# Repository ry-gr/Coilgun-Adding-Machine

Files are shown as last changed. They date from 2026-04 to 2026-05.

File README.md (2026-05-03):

# Coilgun Adding Machine
This is an adding machine, which uses coilguns to carry digits.  
This project was inspired by Matthias Wandel's adding machine, whose posts were an incredible inspiration and resource.  
  
- [Marble adding machine by Matthias Wandel](https://youtu.be/GcDshWmhF4A?si=AagFJ8iIVUzHyiSO)  
- [Further information from his blog](https://woodgears.ca/marbleadd/more.html)  

## TL;DR
The machine is an analog computer that uses marbles to represent bits, and coilguns that shoots the marbles to other columns to carry digits when a bit overflows.  As a note, this project is not finished. I am still working on it actively, but am publishing this preliminarily as my submission for Hack Club: The Game.

## Demo Video (Shows the issue with imprecise positioning)
An issue I am repeatedly running into is having to constantly reposition parts not glued or screw down. I can not get the marble to shoot precisely into the curved part. However this video shows how the logic gates operate and how the machine is capable of charging a capacitor bank, then discharging it by itself. In the video I am performing 1+1 and the marble is unable to properly overflow to get to 2.

https://github.com/user-attachments/assets/430a67ab-8d33-4d41-9ca6-4a4940692cc2

## Schematics

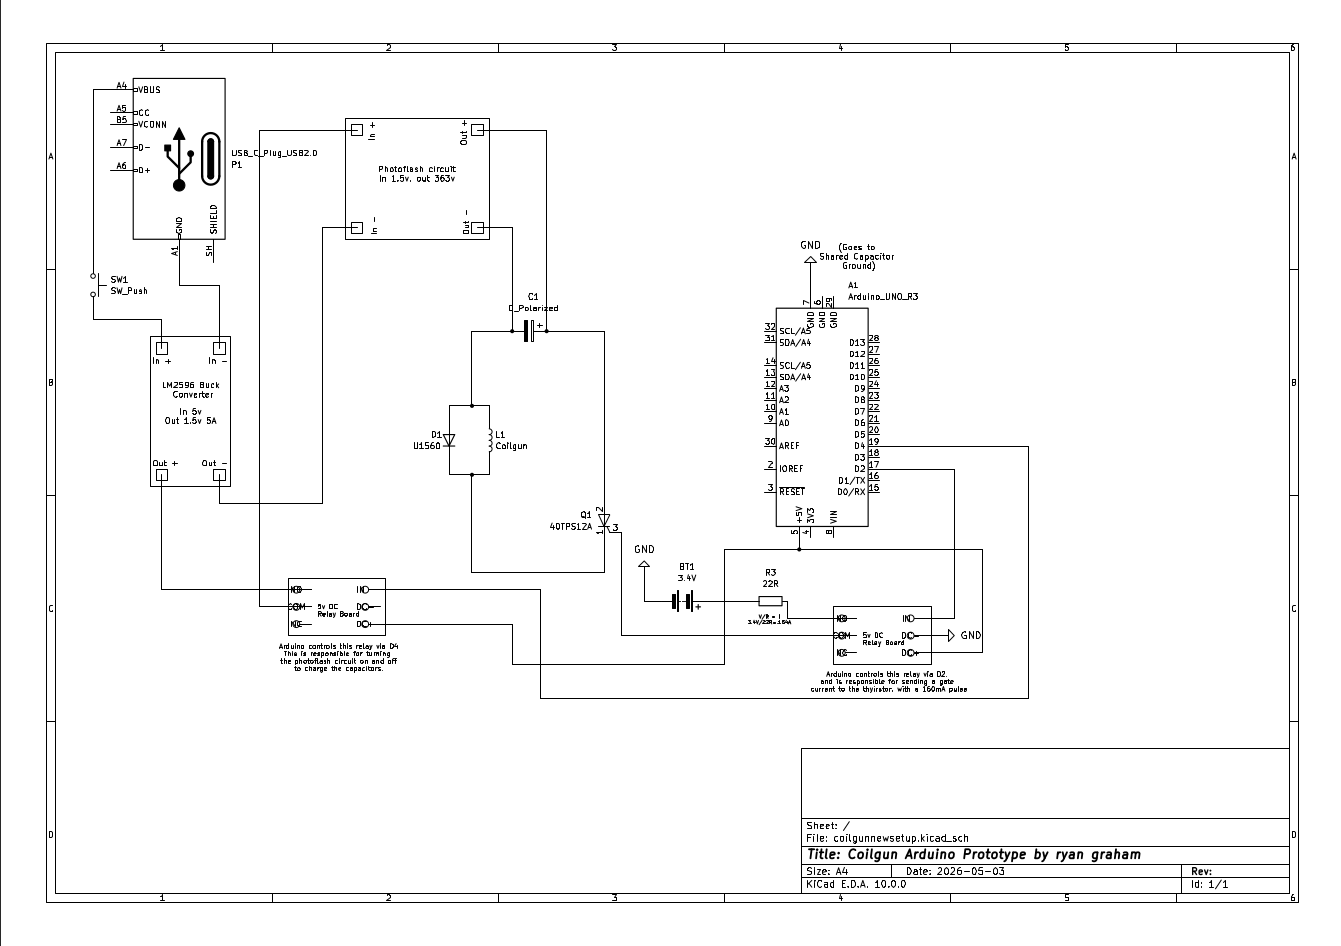
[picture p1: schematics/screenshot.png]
PDF Preview


## FAQ
How does the machine store value?
When the gate is tilted to the left, it has no value. This is the position that all of the gates of the machine start in. 
   
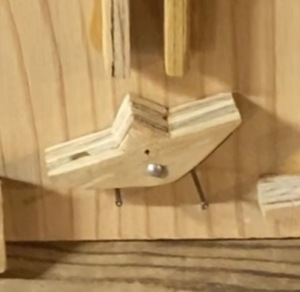
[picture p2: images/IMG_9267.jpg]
noVal


When the gate is tilted to the right, it is storing a value. To determine the value in base 10, you must count how far you are from the far right. The count starts at 0. If this gate was the one furthest to the right, it would be gate 0. 2<sup>0</sup> is 1, so when that gate is tilted to the right, its value is 1. 

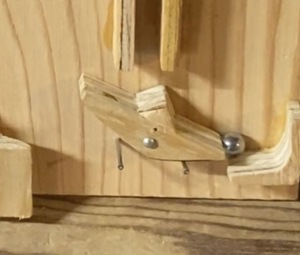
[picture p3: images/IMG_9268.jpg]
holdingVal


# Build Instructions  

> [!CAUTION]
> The voltages needed to accelerate the projectile extremely dangerous and can potentially kill you. I am not saying you shouldn't experiment, but please be very cautious. Have a good multimeter, and know how to use it.

## Part List:
- 40TPS12A Thyristor  
- 2n2222a Transistor  
- 2x 450V 68uF Capacitors  
- USB-C Pinout Board  
- LM2596 Buck Converter (5A)  
- Disposable Camera Flash Circuitry [^1]  
- 24AWG Magnet Wire  
- MUR1560G Diode
- Arduino Uno
- 2x 5v DC Relays  

## How to prepare the disposable camera
You will need to completly strip the disposable camera of its housing, I did this by jamming a flat head screwdriver in the side, cutting all the adhesive holding it together and then popping the clips. The board is basically the only electronic component in the whole thing, so it should be easy to see. You should see a cylindrical capacitor connected to the board. Measure the voltage, and if it is charged (carefully) discharge it with a screwdriver that has a non metallic handle. Then pop out the entire module gently. Mark the board on the connector that the capacitors stripe is. That is the negative output terminal. Now desolder the capacitor, and set it to the side. I did not use the capacitor as it didnt have enough voltage for my project, but it is still a useful component. The next is figuring out how make your board stay triggered. Some have a button that you can pry off, then scratch the pcb coating off to bridge the pins, others you can solder the moveable component in place to permanently set it. 

## Operating Principle of the Electronics
The USB-C is connected to power, supplying 5v, which gets converted to 4.5V with the Buck Converter. This goes to the input of the camera flash circuitry, (technically the flash circuit only accepts 1.5v, but supplying it more makes it charge faster). From there it goes to the capacitors which are wired in parallel to make a 900V Capacitor. Boom, now after about 15seconds of charging we stop, and send a signal from the arduinos digital output. But uh-oh the arduino cant trigger the beefy 40TPS12A by itself, so that gets amplified big time to 200mA with the NPN transistor. Now the signal arrives at the gate, and the once open circuit closes. In an instant the current from the capacitors flows through the thyristor into the coilgun, where it rapidly creates a powerful electromagnetic field around the coil. This Field applies force to the steel .25inch ball sitting at the base of the coil, and the force overpowers gravity accelerating the ball to the coils core. Just as quickly the voltage source shuts off, the capacitors are now empty and the ball flies into the air with velocity. But wait, what about Faradays Principle? With the voltage cut, the coil wants very badly to continue the current it was once conducting so it send a massive voltage spike in the oppposite direction to try to get some more. But now the big boy diode, which is reverse biased awakes from its sleep and the massive voltage spike is consumed as mere heat by the didoe. Just that quickly we have consumed 380V. 


## Operating Principle of the Adding Machine
As explained in Mattias's Video, the machine originally holds 0. Each gate represents a number. Starting from the right, it goes from 2^0, then the gate to its left is 2^1. The one to the left of that is 2^2. This can go on forever. By using the definition of binary numbers, we can add numbers. 
For example: We put a marble into the empty machine on the furthest gate to the right. The rocker tilts and the marble is stuck. The internal value of the machine is now 2^0 = 1. We add a marble to the second gate, and it gets stuck there. By adding this we have added 2^1 = 2, to the internal value of the machine. So in total we have 2+1=3 in value. Now adding another marble to the furthest gate to the right, and whcih tilts the rocker discarding the stuck marble, and shooting the marble to the second gate, which does the same and shoots the marble to the third gate. Now our internal value is 2^2=4. We added 2+1+1, and the machine shows the final value.


## Data Collection and optimization
Coilguns attract ferromagnetic objects to their core while they have current. This is great although if we get our projectile to get attracted to the core, and have velocity but then be pulled backwards by the coilgun. So we need to precisely time when we shut voltage off, so we dont pull our projectile backwards. In lieu of a IR system, to measure the interruption, I decided to precisely time the charging of capacitor, so they will simply run out of voltage when the projectile is at its core and no longer should have an attraction. By measuring the time the projectile charged for, the voltage of the capacitor, and the height the projectile went I came up with this graph. I was charging the capacitors externally with the flash circuit, and manually timing everything, so there might be imprecision, but it gives a rough estimate of where we need to be.  
<sub>A quick note about why I decided to use time instead of voltages to trigger the discharge: I created several iterations of voltage dividers that connected the capacitor to an arduino analog pin. I was able to sucessfully read capacitor voltages, but doing this made a slow bleed from the resistors, which interfered with the charging circuit.</sub>

## Raw Data
| Voltage (V) | Time (sec) | Height (in) |
|---|---|---|
| 363 | 19.63 | 12.5 |
| 469 | 23.54 | 12 |
| 444 | 21.56 | 10 |
| 421 | 20.07 | 10 |
| 375 | 18.38 | 12.5 |
| 408 | 18.71 | 12 |

## Graph


With this data we can conclude somewhere around 18 seconds of charging gives the ideal height. Voltages of 360-375 seemed perfect. 
Now I will add a relay to my circuit so the arduino can precisely control charging and I can run precise experiments with the timing.
There are 2 relays I will add: 1 that is responsible for triggering the disposable camera charger. That simply interrupts and connects the positive terminal of the buck converter connected to it, to turn it on and off.
The other relay is connected to an external power supply, connected to a resistor that limits current to approx 160mA then connected to the thyristors gate. That relay is responsible for triggering the thyristor. 

## This project is unfinished. This is where I got to, but I am unable to get the coilgun to shoot the marble as high as it should go. I am actively investigating how to fix that, but I suspect either overvolting the disposable camera charging is introducing an issue, and or by my capacitor bank is fried after accidental abuse, and I simply need to switch with fresh ones. 
This is not the end of this project, but I am publishing it in its unfinished state so I can qualify for Hack Club the Game. 
You haven't seen the end of this yet!

[^1]: How do you get disposable camera circuitry for free? Used disposable cameras have a lot of handy parts, like a high voltage capacitor, and circuitry that steps up 1.5v to 363v. That circuitry is very helpful and I use it in this build. To get them for free, I found places that sell and process film from disposable cameras around me, and went in and asked for them. They were more than happy to give them out to me, and i've tried this at a few spots, where I often got 30 used cameras per visit. Primarily I use the flash circuitry from FujiFilm QuickSnaps, as they are reliable and plentiful.

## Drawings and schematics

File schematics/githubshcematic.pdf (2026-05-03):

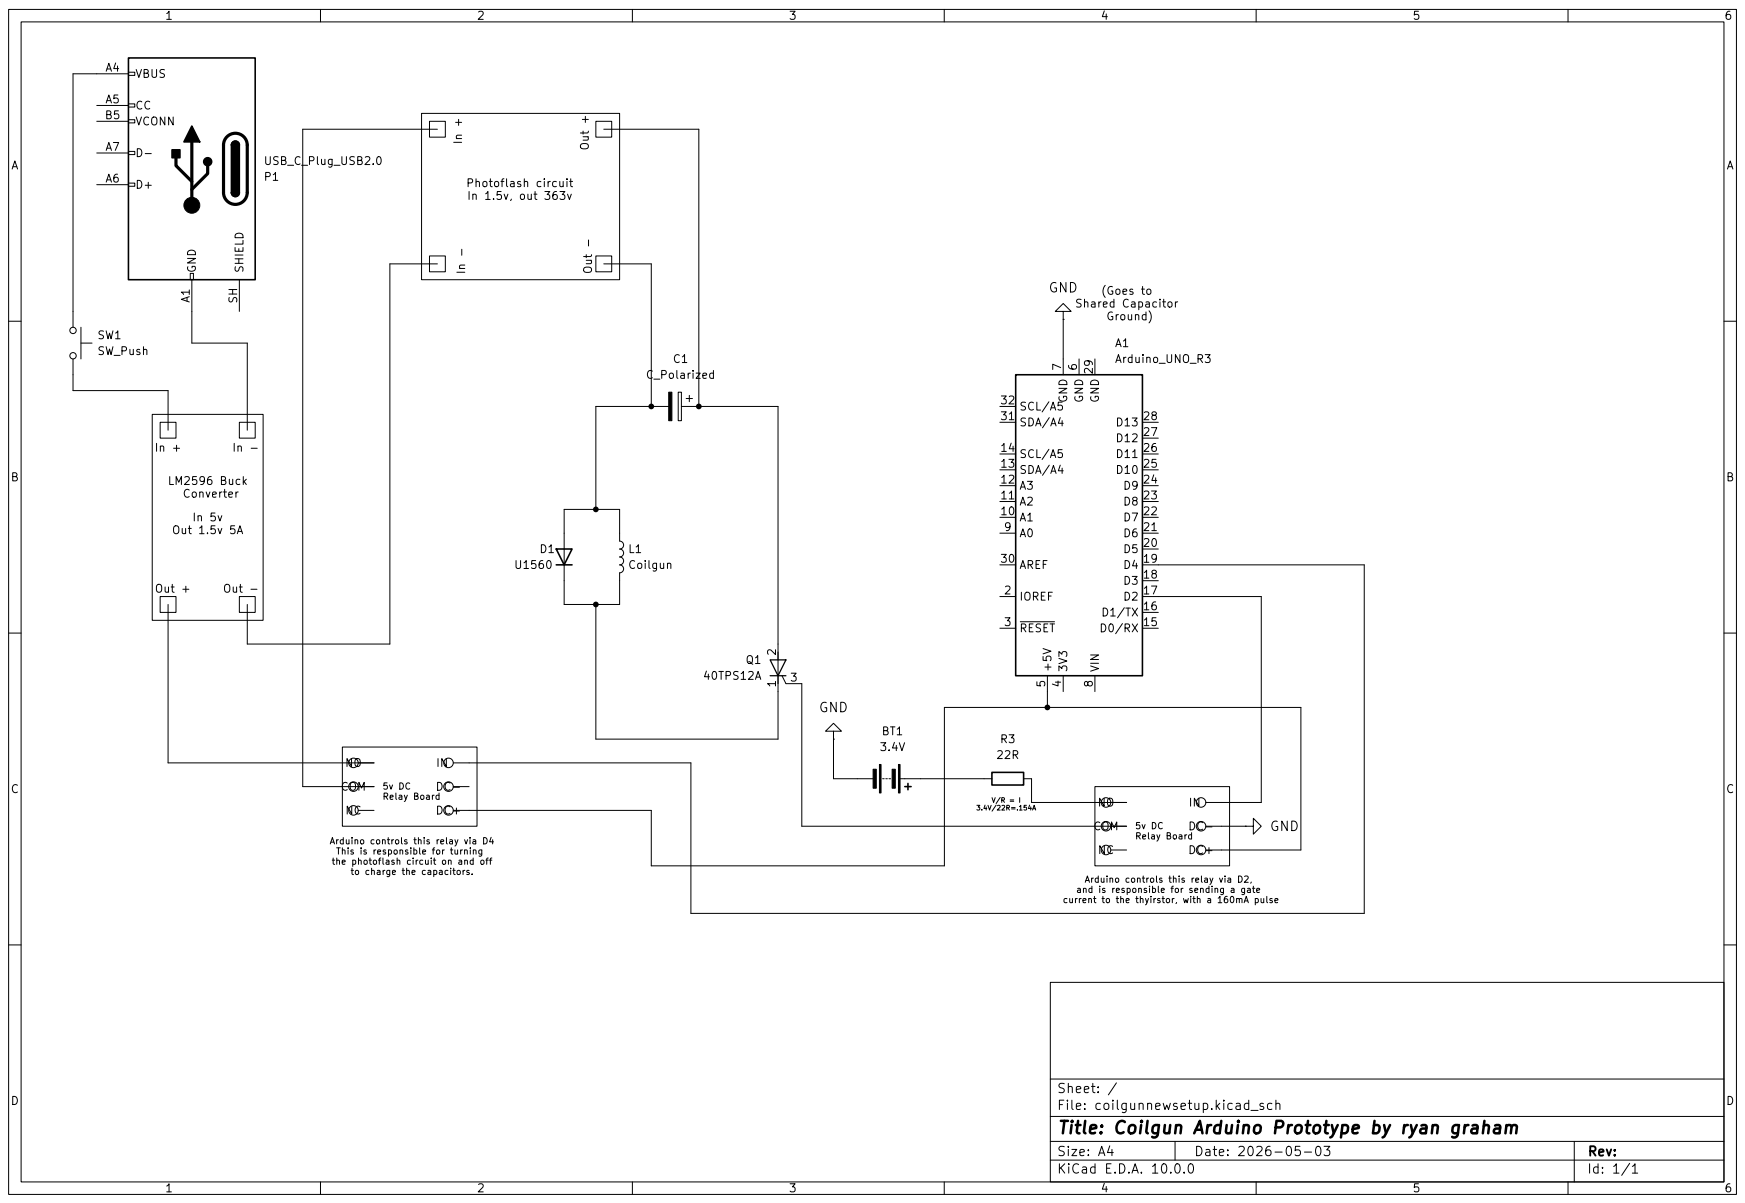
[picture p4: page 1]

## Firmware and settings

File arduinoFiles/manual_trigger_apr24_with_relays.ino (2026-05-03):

void setup() {
  // put your setup code here, to run once:
  Serial.begin(9600);
  pinMode(4, OUTPUT); //trigger pin for charging relay
  pinMode(2, OUTPUT); //trigger pin for thyristor relay

  digitalWrite(4, LOW);

}

void loop() {
  // put your main code here, to run repeatedly:
  int del;
  if (Serial.available() > 0) 
  { 
    String input = Serial.readString();
    input.trim();
    Serial.println(input);

    if(input.equals("go"))
    {
      digitalWrite(4, HIGH); //turns on charging relay, letting capacitor start to charge
      Serial.println("charging cap");
      del = 20000; //how much should the capacitor charge? 
      for(int i = 0; i<4; i++)
      {
        delay(del/4);
        Serial.print((25*(i+1)));
        Serial.println("% of the way charged");
        //simple charging progress loop
      }
      digitalWrite(4, LOW);
      

      digitalWrite(2, HIGH); //triggers thyristor relay allowing the thyristor to close and the coil to fire
      Serial.println("discharged capacitor");
      delay(10); //latches for 10ms
      digitalWrite(2, LOW);
    }

    if(input.equals("charge"))
    {
      digitalWrite(4, HIGH); //turns on charging relay, letting capacitor start to charge
      Serial.println("charging cap");
      del = 25000; //how much should the capacitor charge? 
      for(int i = 0; i<4; i++)
      {
        delay(del/4);
        Serial.print((25*(i+1)));
        Serial.println("% of the way charged");
        //simple charging progress loop
      }
      digitalWrite(4, LOW);

    }
    if(input.equals("fire"))
    {
      digitalWrite(2, HIGH); //triggers thyristor relay allowing the thyristor to close and the coil to fire
      Serial.println("discharged capacitor");
      delay(10); //latches for 10ms
      digitalWrite(2, LOW);
    }
  }
}

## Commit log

2026-04-24 Revise caution message and electronics explanation
    Updated cautionary note about dangerous voltages and clarified the operating principle of the electronics.
2026-04-24 Format note in README with subscript
    Added subscript formatting to a note about timing vs voltage for triggering discharge.
2026-04-24 Improve README clarity on marble machine and coilgun
    Clarified the explanation of the marble machine and updated the data collection section regarding coilgun operation and capacitor timing.
2026-04-24 Revise caution message for voltage dangers
    Updated cautionary note regarding dangerous voltages in the README.
